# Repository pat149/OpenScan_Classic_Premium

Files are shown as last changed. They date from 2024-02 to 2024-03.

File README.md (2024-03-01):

# OpenScan Classic Premium
Completely redesigned version of the OpenScan Classic by Thomas Megel ([ @github/OpenScan-org ](https://github.com/OpenScan-org)).

> [!CAUTION]
> This version is still work in progress. There's no guarantee everything works as intended. I'm expecting to do the full testing until the middle of February.

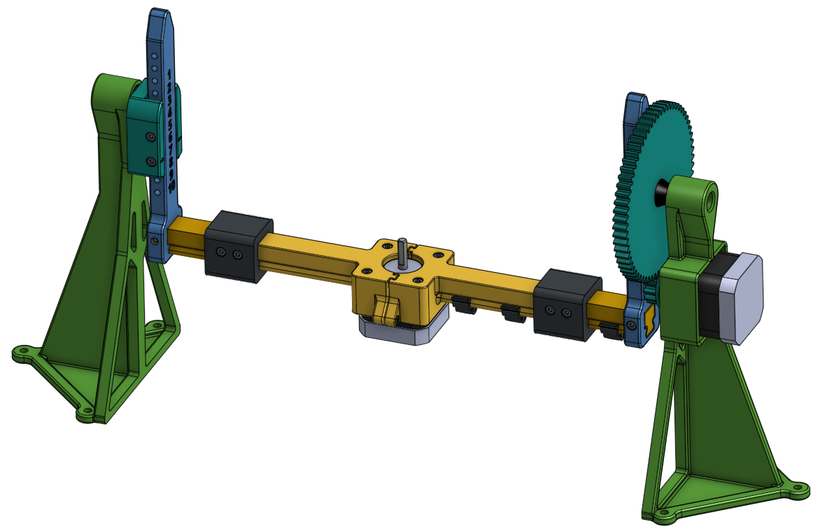
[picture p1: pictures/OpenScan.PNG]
OpenScan Classic Premium


## Introduction
The intentions behind the redesign of the OpenScan Classic were that it seems it has never gotten out of it's prototype stage constructionwise.
So I made a list with things that should be improved.

- sturdier overall construction
- more convenient height adjustment
- use ball bearings instead of pins
- use heated inserts instead of driving the screw into the plastic
- higher modularity concerning the size of the scanner
- cable management for the turntable stepper
- printing without any supports
- higher quality looking finish

So I redesigned the Classic version from scratch on and the result was the OpenScan Classic Premium (might change the name in the future). No parts of the original mainframe have been reused in order to make room for improvements while simultaneously keeping the original shape and functionality.
Because I don't use a PiCam I didn't redesigned the stand for the Raspberry Pi (yet).

## Bill of material
This BOM represents the bare minimum of material without using any extensions on the arms.
| Part  | Quantity |
| --- | --- |
| M3x8 (ISO 4762) | 8  |
| M3x10 (ISO 4762) | 2  |
| M3x25 (ISO 4762) | 2  |
| M3x30 (ISO 4762) | 4  |
| M5x20 (ISO 4762) | 1  |
| M5x25 (ISO 4762)| 1  |
| Washer M5  | 2  |
| Heated Insert M3x4  | 8  |
| Heated Insert M5x6  | 2  |
| Ball bearing 625-2RS  | 4  |
| Nema 17 Stepper Motor (>13Ncm)  | 1  |
| Nema 17 Stepper Motor (>40Ncm)  | 1  |
| Stand1_Nema17.step  | 1  |
| Stand2.step  | 1  |
| Spacer_Adapter_Gear.step (Measure shaft stick out for correct version)  | 1  |
| Gear_Small.step  | 1  |
| Adapter_Gear.step  | 1  |
| Adapter.step  | 1  |
| Rotary_Arm.step  | 2  |
| Turntable_Base1.step  | 1  |
| Turntable_Base2.step  | 1  |

## Print settings
Every part can be printed without any supports at all using the following print settings:
- 0.4mm nozzle
- 0.2mm layer height
- 3 walls (except for Turntable_Base, Turntable_Extension and Rotary_Arm: min. 5 walls, depending on the overall length)
- 15% infill

## Assembly instructions
For a detailed step by step instruction go to the dedicated instructions folder above.
For those only interested in the assembly order here are some exploded views of the OpenScan Classic Premium.

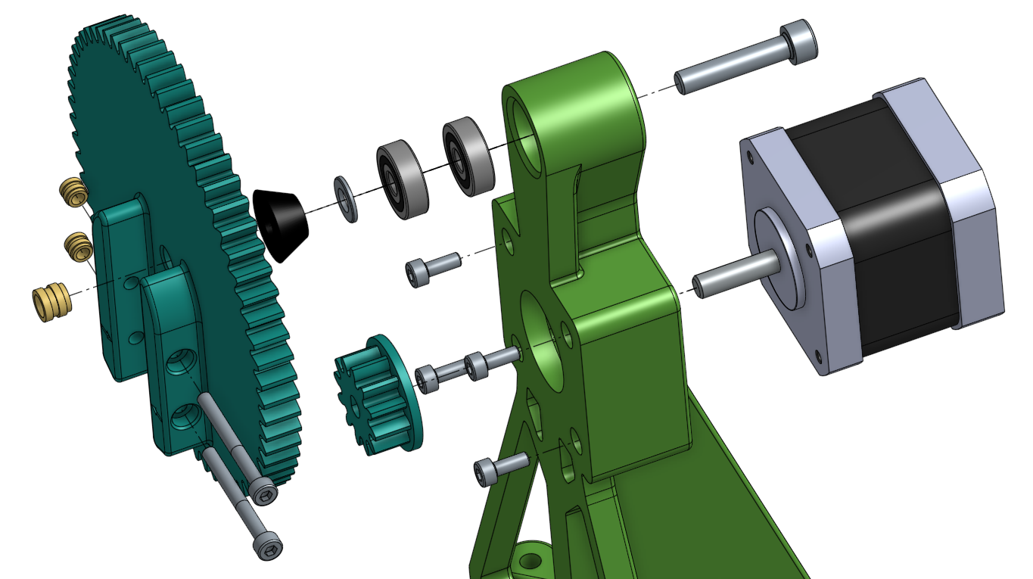
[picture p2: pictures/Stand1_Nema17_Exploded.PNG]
Assembly of the motor stand

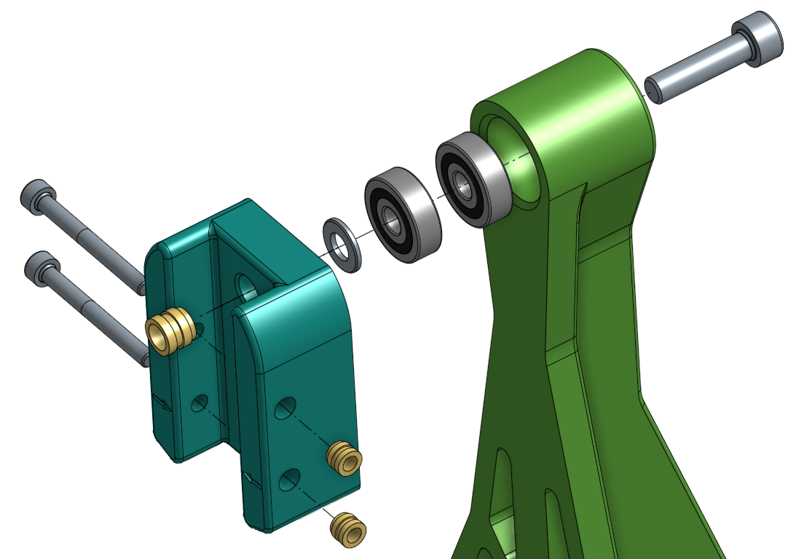
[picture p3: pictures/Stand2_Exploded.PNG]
Assembly of the stand 2

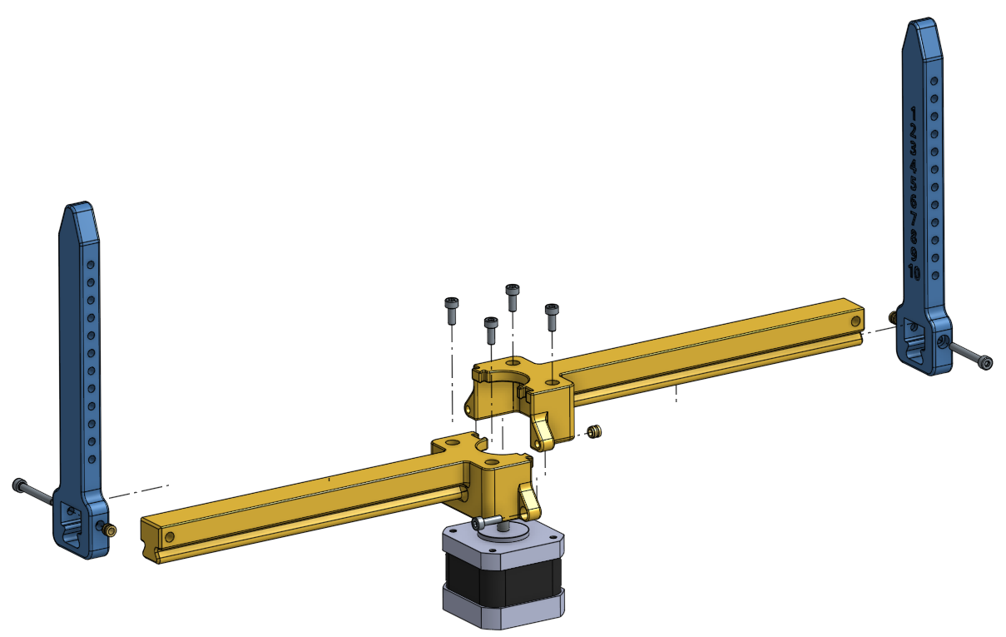
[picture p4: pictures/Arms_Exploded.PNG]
Assembly of the arms


## To-do-list
- [ ] Adding more rigidity to the turntable stepper frame mount
- [ ] Create a heavy duty version

## Changelog
- 1st March, 2024: reuploaded all *.stl with correct scale

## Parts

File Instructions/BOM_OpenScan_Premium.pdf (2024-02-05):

Description | Quantity
Hex socket head screw M3x8 | 8
Hex socket head screw M3x10 | 2
Hex socket head screw M3x25 | 2
Hex socket head screw M3x30 | 4
Hex socket head screw M5x20 | 1
Hex socket head screw M5x25 | 1
Washer M5 | 2
Heated Insert M3x4 | 8
Heated Insert M5x6 | 2
Ball bearing 625-2RS | 4
Nema 17 Stepper Motor (>13Ncm) | 1
Nema 17 Stepper Motor (>40Ncm) | 1
Stand1_Nema17.step | 1
Stand2.step | 1
Spacer_Adapter_Gear.step (Measure shaft stick out for correct version) | 1
Gear_Small.step | 1
Adapter_Gear.step | 1
Adapter.step | 1
Rotary_Arm.step | 2
Turntable_Base1.step | 1
Turntable_Base2.step | 1

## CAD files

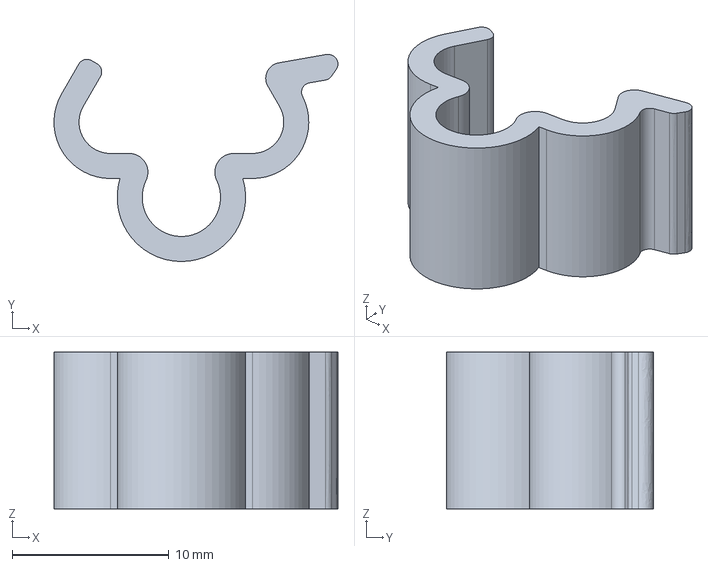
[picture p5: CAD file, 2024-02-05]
STEP/Cable_Clip.step
18.1 x 13.2 x 10.0 mm

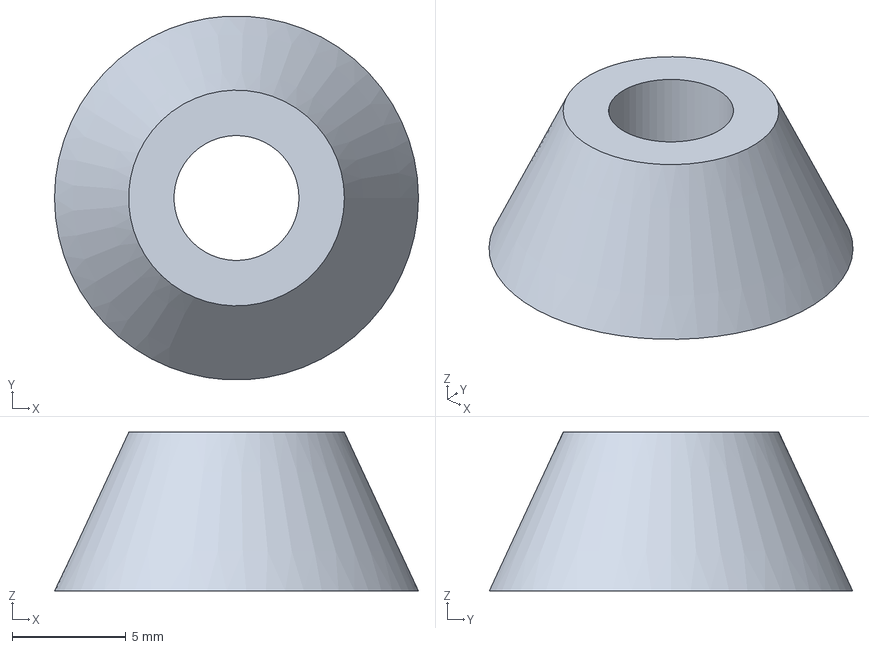
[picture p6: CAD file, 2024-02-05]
STEP/Spacer_Adapter_Gear/Spacer_Adapter_Gear_15mm.step
16.0 x 16.0 x 7.00 mm

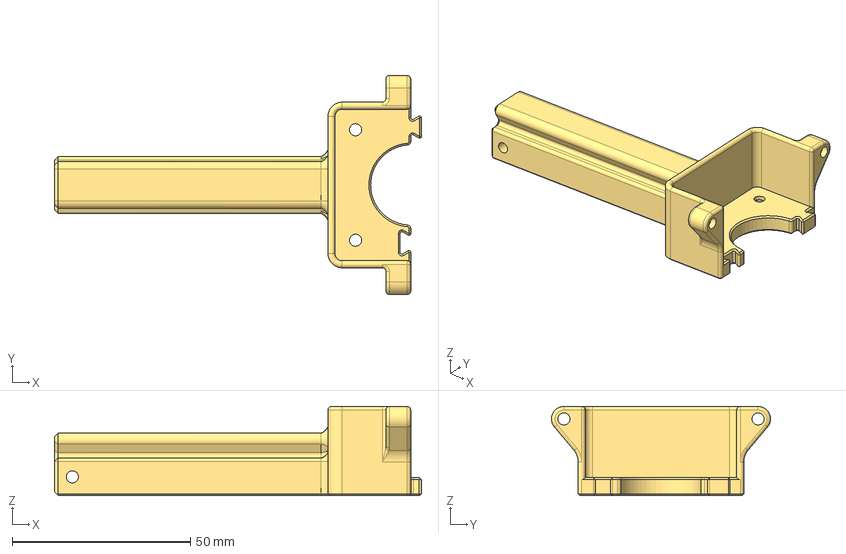
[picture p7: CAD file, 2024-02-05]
STEP/Turntable_Base1/Turntable_Base1_100mm.step
103.0 x 61.5 x 25.0 mm

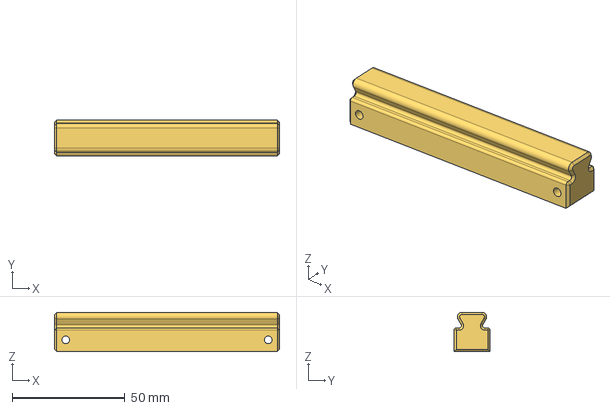
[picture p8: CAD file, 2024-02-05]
STEP/Turntable_Extension/Turntable_Extension_100mm.step
100.0 x 16.0 x 17.5 mm

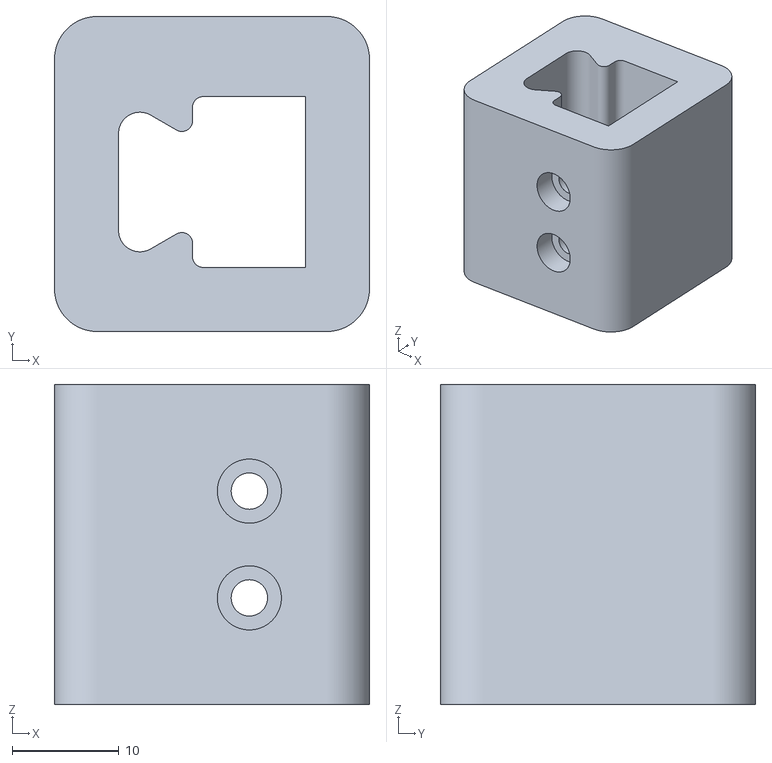
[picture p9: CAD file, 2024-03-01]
STL/Extension_Connector.stl
29.5 x 29.5 x 30.0

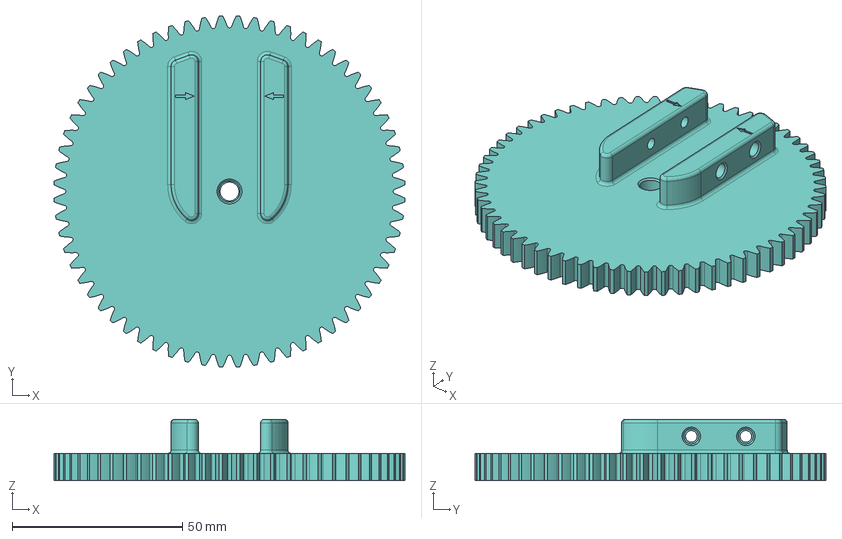
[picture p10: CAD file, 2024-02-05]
STEP/Adapter_Gear.step
103.0 x 103.0 x 18.0 mm

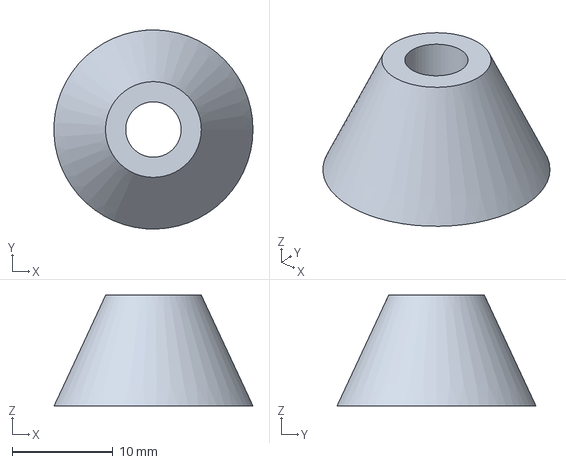
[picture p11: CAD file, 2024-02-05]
STEP/Spacer_Adapter_Gear/Spacer_Adapter_Gear_19mm.step
19.7 x 19.8 x 11.0 mm

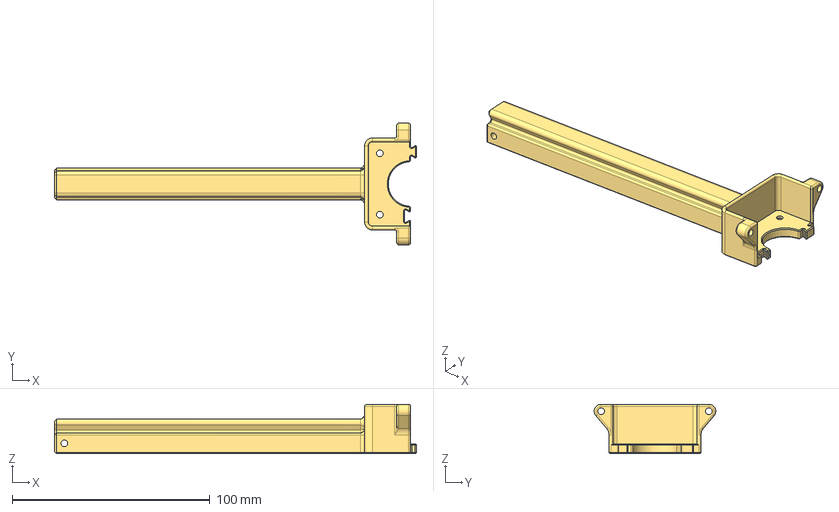
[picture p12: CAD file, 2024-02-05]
STEP/Turntable_Base1/Turntable_Base1_180mm.step
183.0 x 61.5 x 25.0 mm

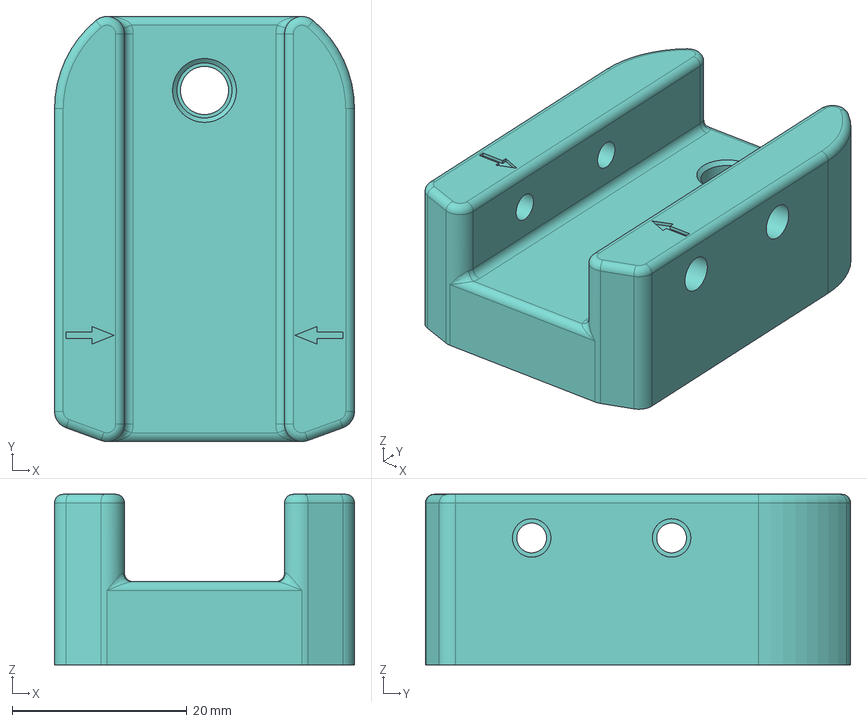
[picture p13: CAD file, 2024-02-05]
STEP/Adapter.step
34.3 x 48.6 x 19.5 mm

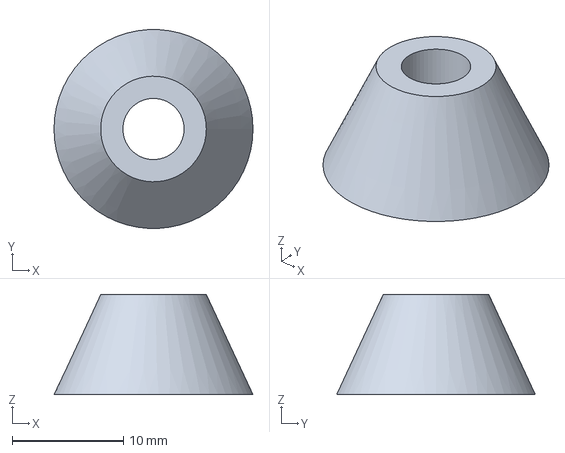
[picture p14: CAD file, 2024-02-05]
STEP/Spacer_Adapter_Gear/Spacer_Adapter_Gear_17mm.step
17.9 x 17.9 x 9.00 mm

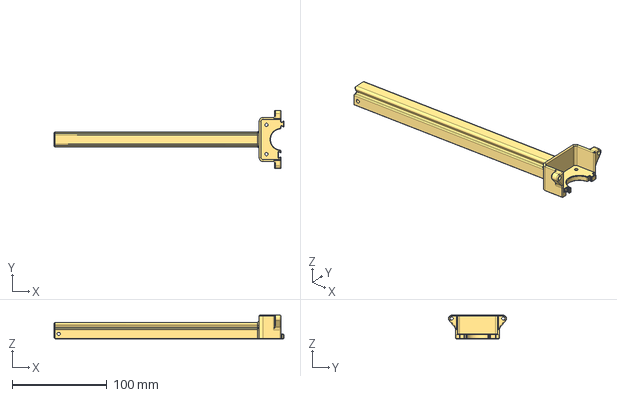
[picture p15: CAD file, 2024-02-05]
STEP/Turntable_Base1/Turntable_Base1_240mm.step
243.0 x 61.5 x 25.0 mm

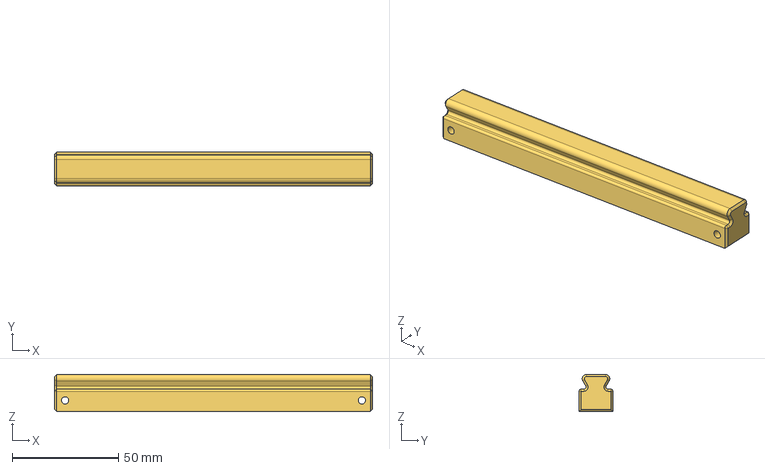
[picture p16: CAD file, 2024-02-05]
STEP/Turntable_Extension/Turntable_Extension_150mm.step
150.0 x 16.0 x 17.5 mm

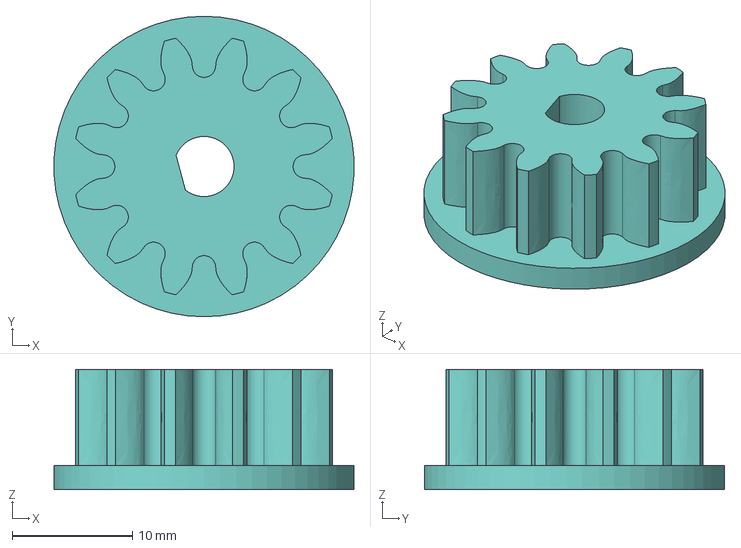
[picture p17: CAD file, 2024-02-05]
STEP/Gear_Small.step
25.0 x 25.0 x 10.0 mm

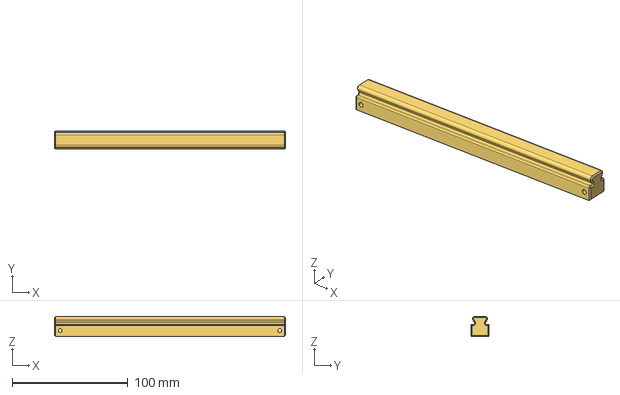
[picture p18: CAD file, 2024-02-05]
STEP/Turntable_Extension/Turntable_Extension_200mm.step
200.0 x 16.0 x 17.5 mm

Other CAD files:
STEP/Turntable_Base2/Turntable_Base2_100mm.step
STEP/Turntable_Base2/Turntable_Base2_180mm.step
STEP/Turntable_Extension/Extension_Connector.step
STEP/Turntable_Base2/Turntable_Base2_240mm.step
STEP/Rotary_Arm.step
STEP/Stand1_Nema17.step
STEP/Stand2.step
STEP/Turntable_Extension/Turntable_Extension_50mm.step
STL/Adapter.stl
STL/Adapter_Gear.stl
STL/Cable_Clip.stl
STL/Gear_Small.stl
STL/Rotary_Arm.stl
STL/Spacer_Adapter_Gear/Spacer_Adapter_Gear_15mm.stl
STL/Spacer_Adapter_Gear/Spacer_Adapter_Gear_17mm.stl
STL/Spacer_Adapter_Gear/Spacer_Adapter_Gear_19mm.stl
STL/Turntable_Base1/Turntable_Base1_240mm.stl
STL/Turntable_Extension/Turntable_Extension_100mm.stl
STL/Turntable_Extension/Turntable_Extension_150mm.stl
STL/Turntable_Extension/Turntable_Extension_200mm.stl
STL/Turntable_Extension/Turntable_Extension_50mm.stl

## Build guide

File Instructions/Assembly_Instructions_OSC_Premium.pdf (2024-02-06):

## Assembly instructions for

# OpenScan Classic Premium

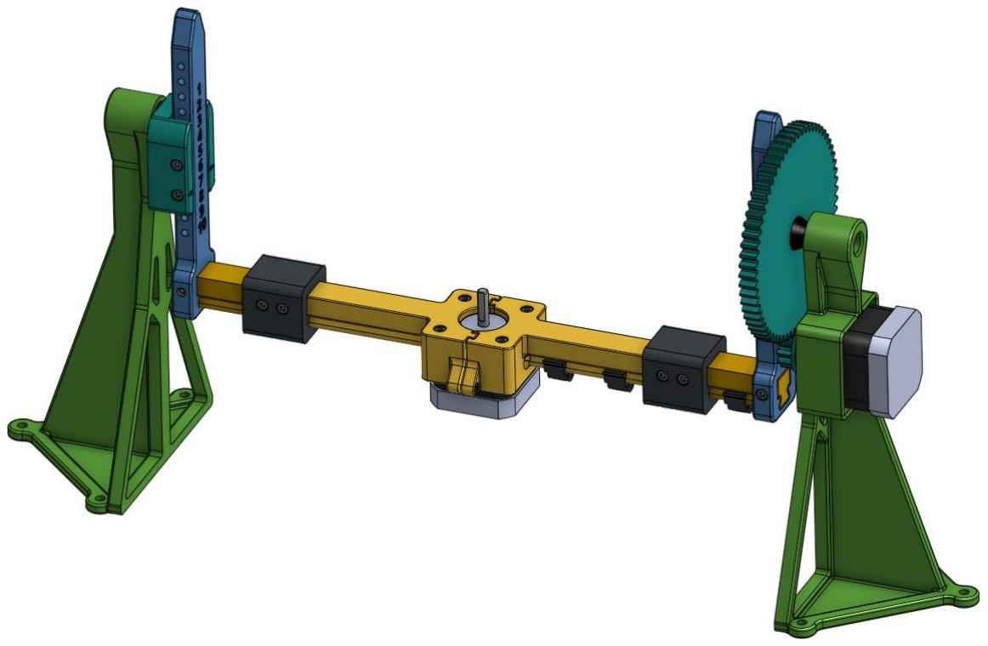
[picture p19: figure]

Description | Quantity
Hex socket head screw M3x8 | 8
Hex socket head screw M3x10 | 2
Hex socket head screw M3x25 | 2
Hex socket head screw M3x30 | 4
Hex socket head screw M5x20 | 1
Hex socket head screw M5x25 | 1
Washer M5 | 2
Heated Insert M3x4 | 8
Heated Insert M5x6 | 2
Ball bearing 625-2RS | 4
Nema 17 Stepper Motor (>13Ncm) | 1
Nema 17 Stepper Motor (>40Ncm) | 1
Stand1_Nema17.step | 1
Stand2.step | 1
Spacer_Adapter_Gear.step (Measure shaft stick out for correct version) | 1
Gear_Small.step | 1
Adapter_Gear.step | 1
Adapter.step | 1
Rotary_Arm.step | 2
Turntable_Base1.step | 1
Turntable_Base2.step | 1

# Assembly of the standard version

(assembly of the extensionsions see pages 20-23)

## Bill of material (BOM)

## Overview

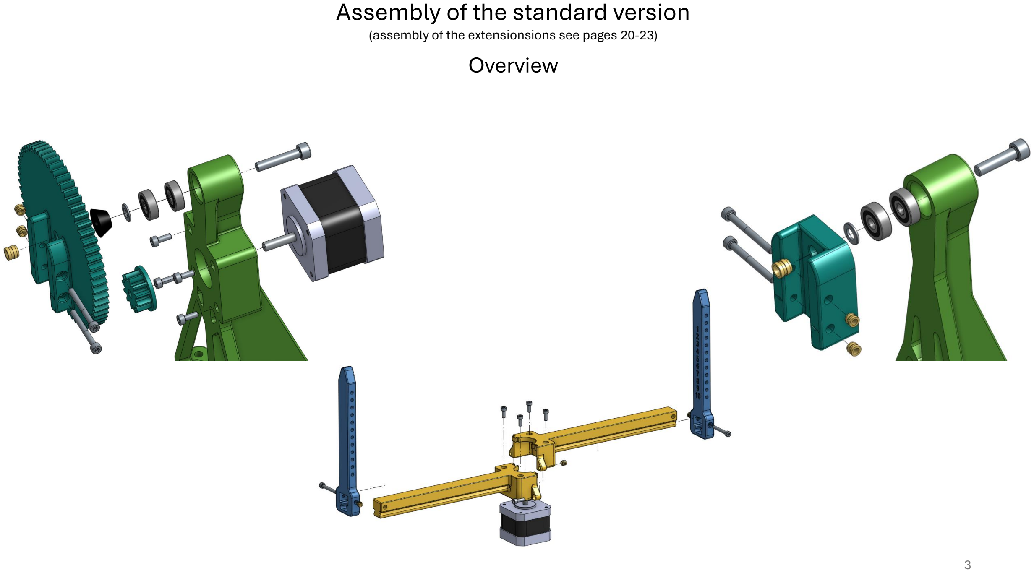
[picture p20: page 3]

(assembly of the extensionsions see pages 20-23)

4x

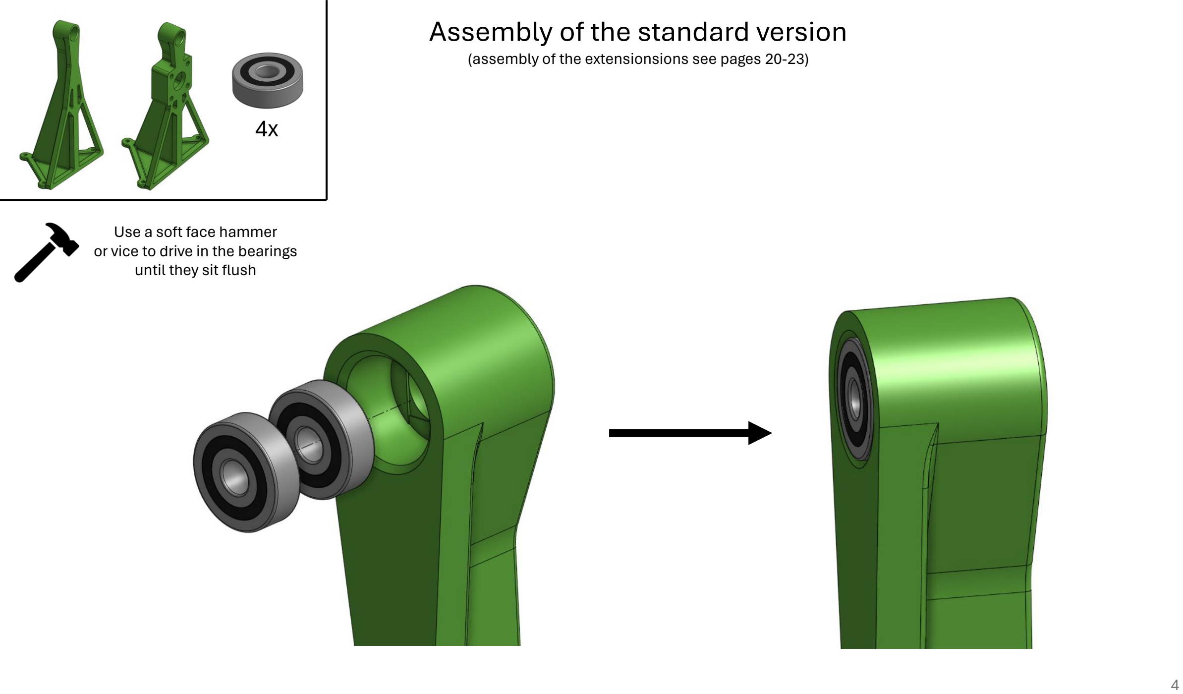
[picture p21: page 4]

(assembly of the extensionsions see pages 20-23)

Use a soft face hammer
or vice to drive in the bearings until they sit flush

(assembly of the extensionsions see pages 20-23)

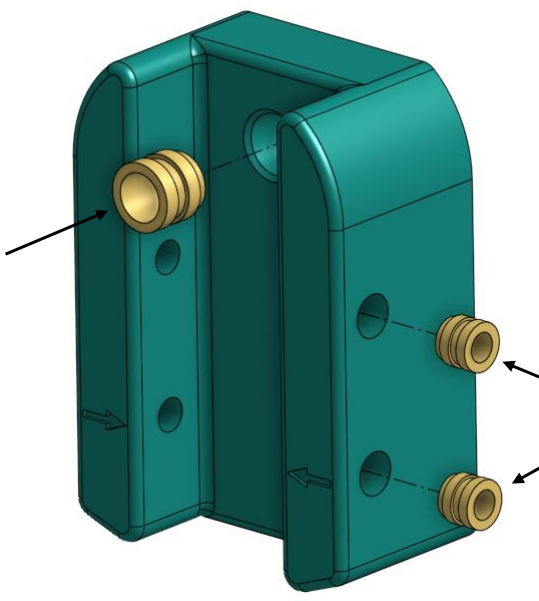
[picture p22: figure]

Use a soldering iron to put in the heated inserts (Temperature: print temperature +10%)

2x
M3x4

1x
M5x6

M5x6

M3x4

(assembly of the extensionsions see pages 20-23)

2x
M3x4
2x

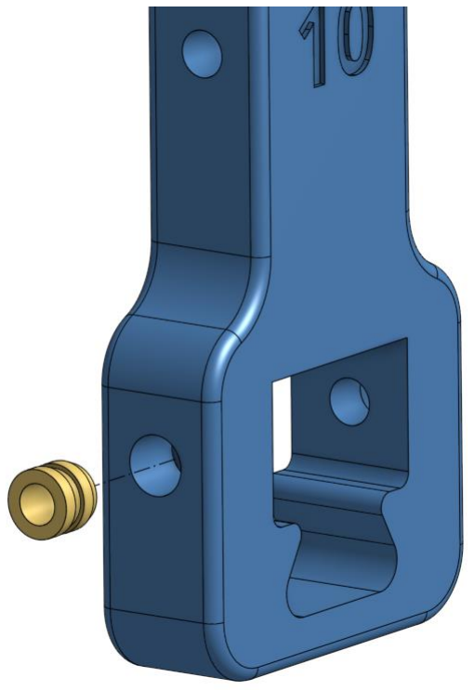
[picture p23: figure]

Use a soldering iron to put in the heated inserts (Temperature: print temperature +10%)

2x
M3x4

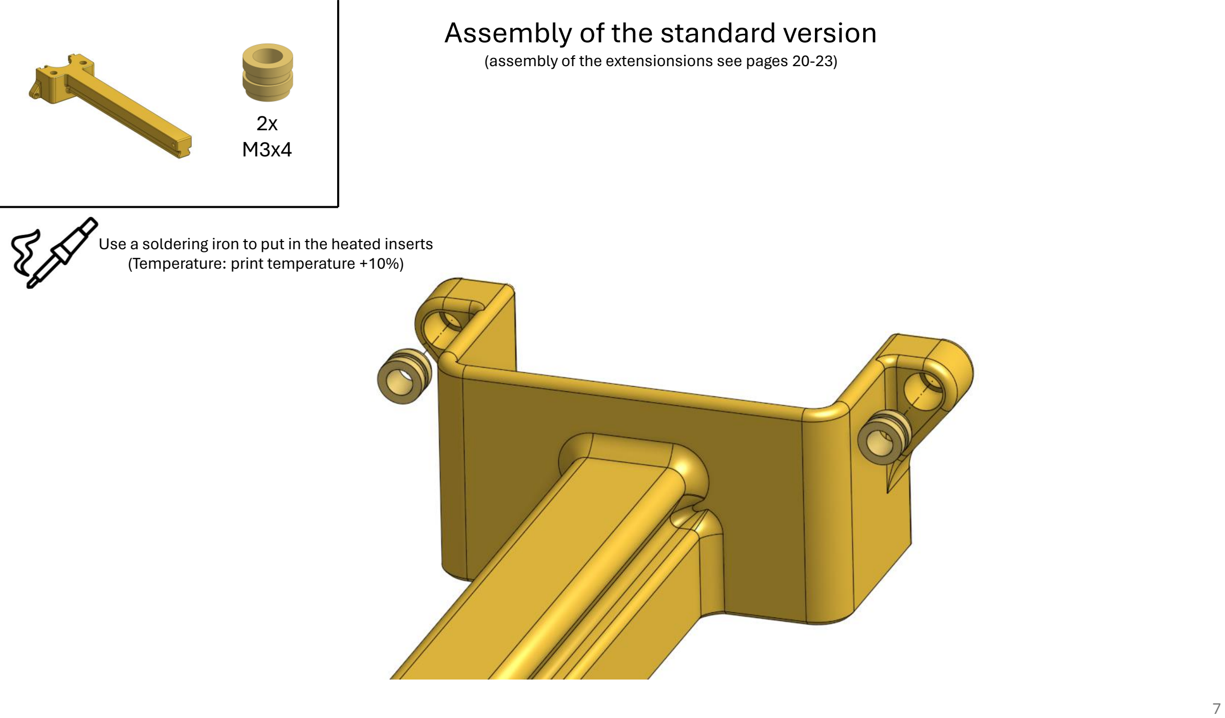
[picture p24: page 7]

(assembly of the extensionsions see pages 20-23)

Use a soldering iron to put in the heated inserts (Temperature: print temperature +10%)

(assembly of the extensionsions see pages 20-23)

2x
M3x4

1x
M5x6

M3x4

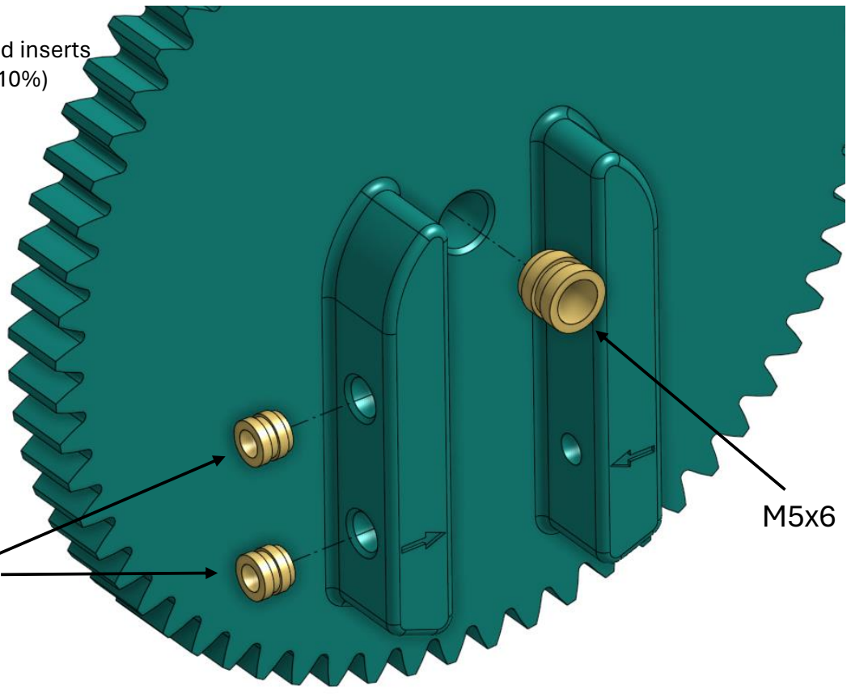
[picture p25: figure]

Use a soldering iron to put in the heated inserts (Temperature: print temperature +10%)

4x

## M3x8 >40 Ncm

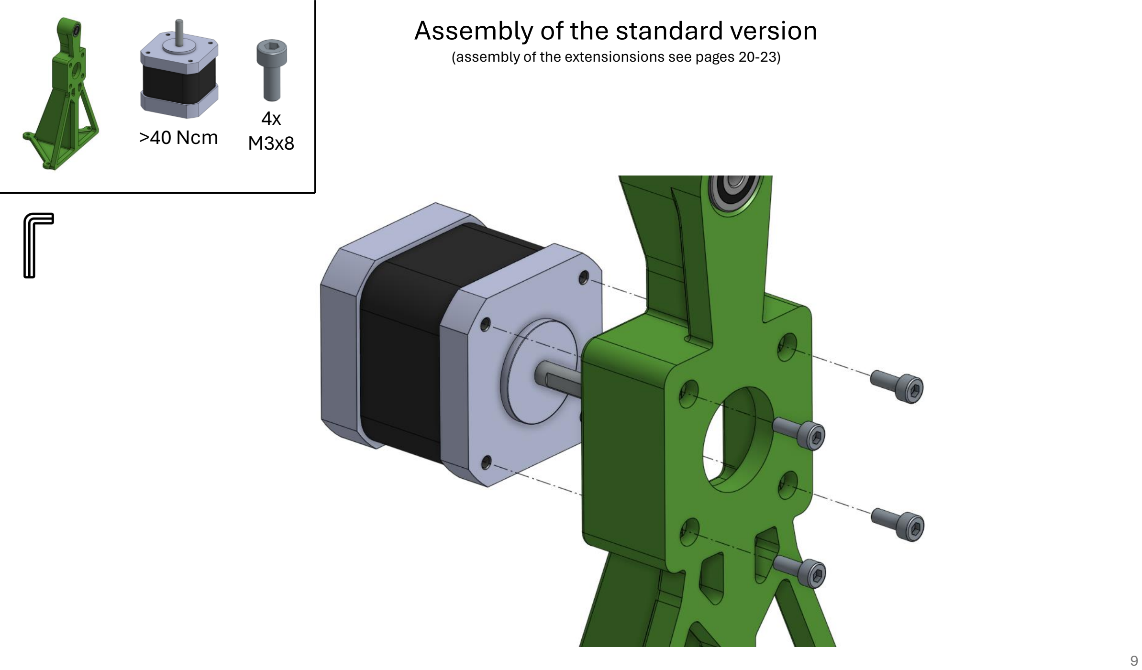
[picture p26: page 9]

(assembly of the extensionsions see pages 20-23)

(assembly of the extensionsions see pages 20-23)

Measure the stick out of the stepper motor shaft from the face of the printed stand.

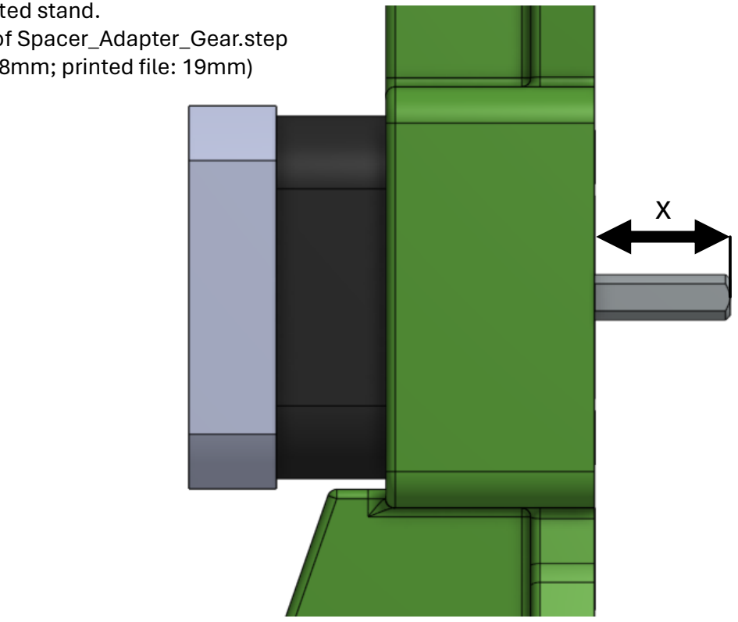
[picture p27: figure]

Print the next bigger version of Spacer_Adapter_Gear.step (e.g. measured value: 17.8mm; printed file: 19mm)

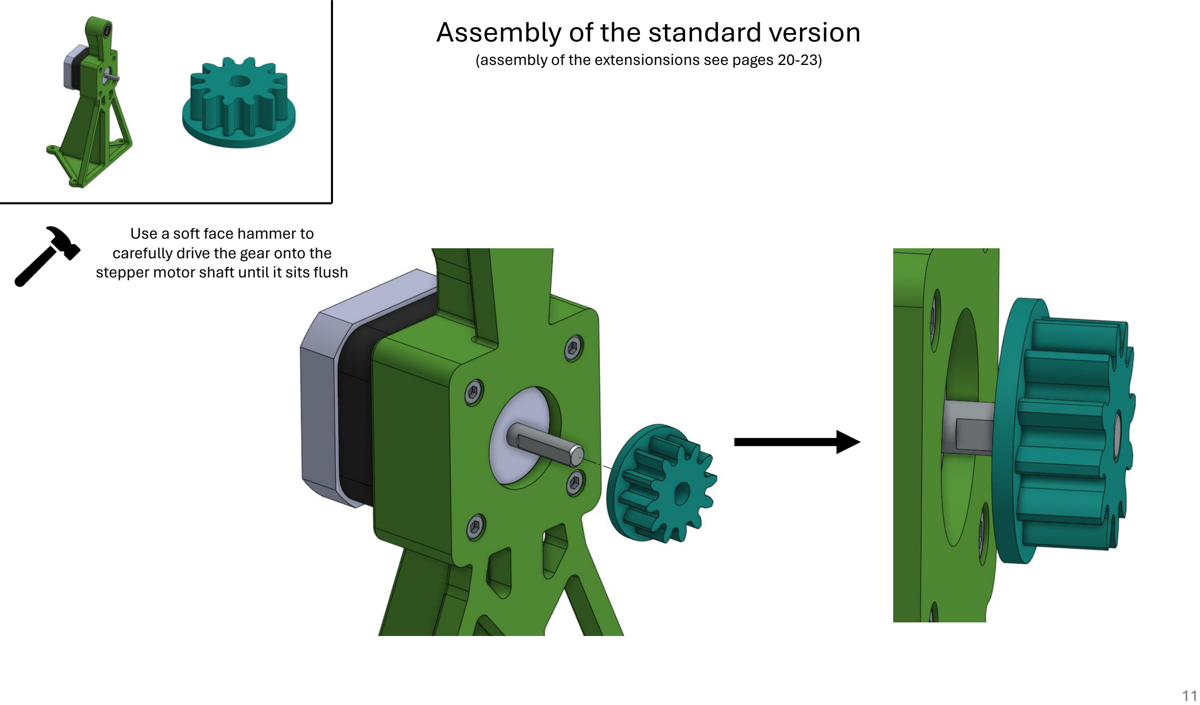
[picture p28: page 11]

(assembly of the extensionsions see pages 20-23)

Use a soft face hammer to
carefully drive the gear onto the stepper motor shaft until it sits flush

M5x25

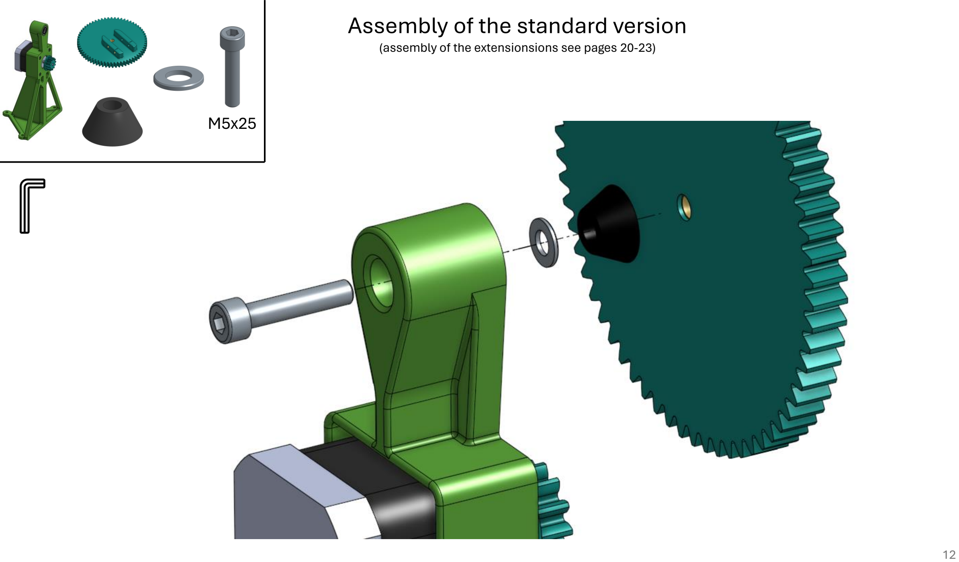
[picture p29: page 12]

(assembly of the extensionsions see pages 20-23)

(assembly of the extensionsions see pages 20-23)

M5x20

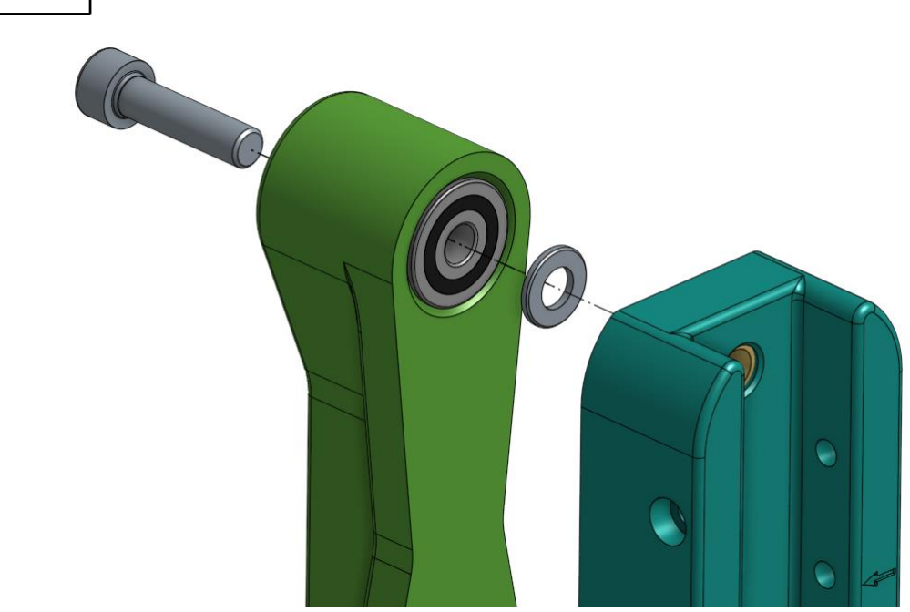
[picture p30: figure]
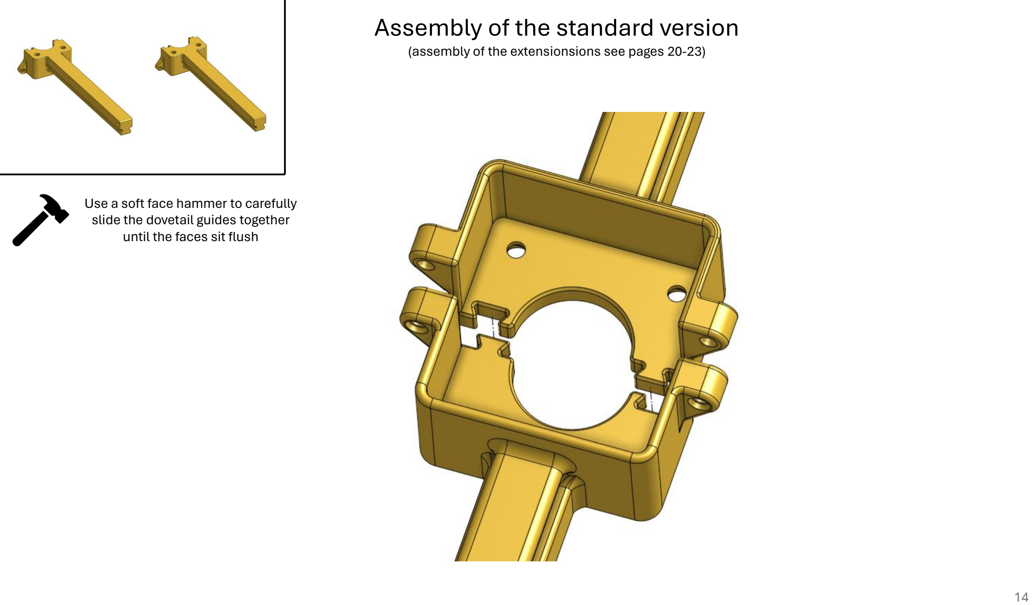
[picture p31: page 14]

(assembly of the extensionsions see pages 20-23)

Use a soft face hammer to carefully slide the dovetail guides together until the faces sit flush

2x
M3x10

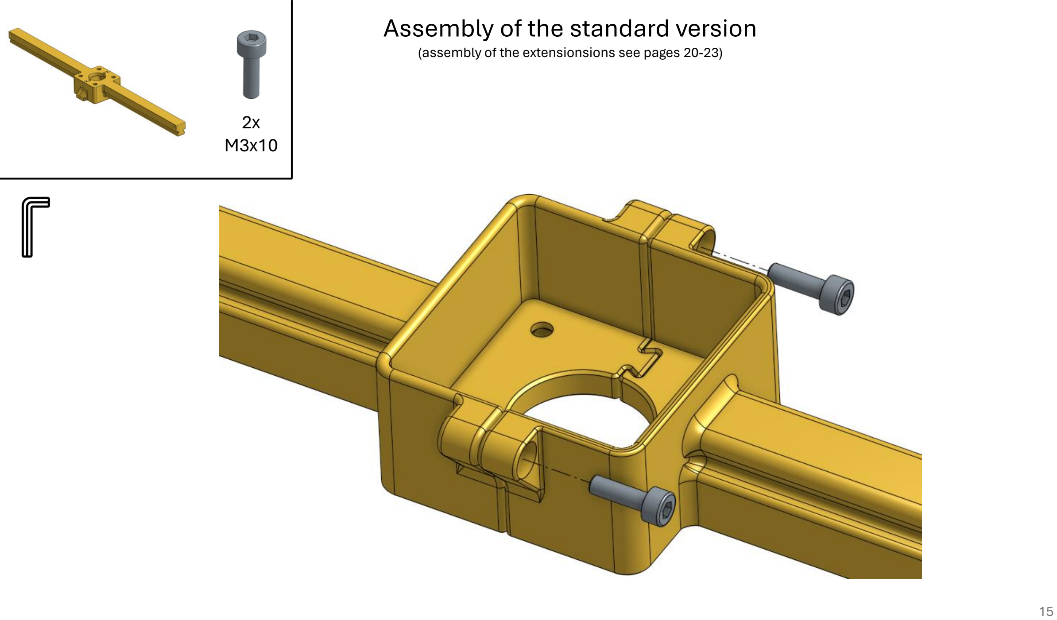
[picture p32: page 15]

(assembly of the extensionsions see pages 20-23)

(assembly of the extensionsions see pages 20-23)

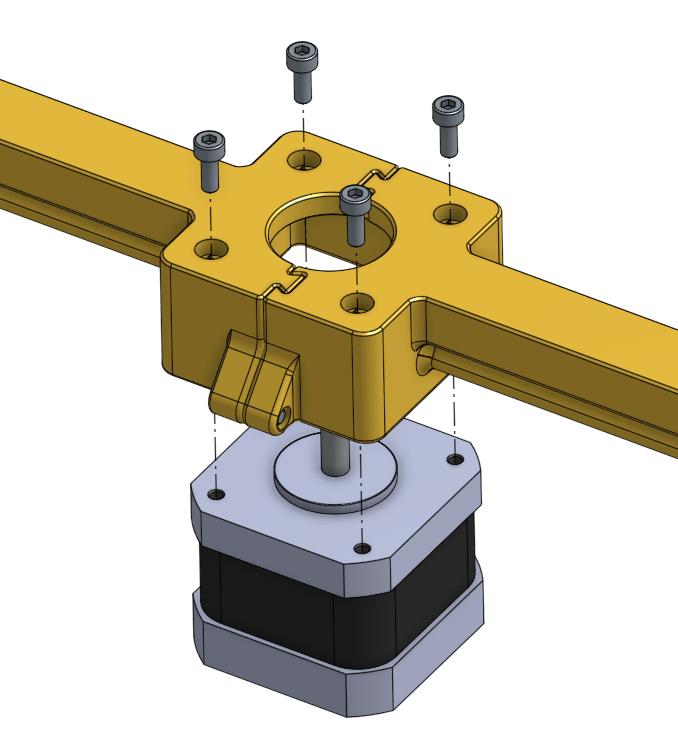
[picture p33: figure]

4x

## M3x8 >13 Ncm

(assembly of the extensionsions see pages 20-23)

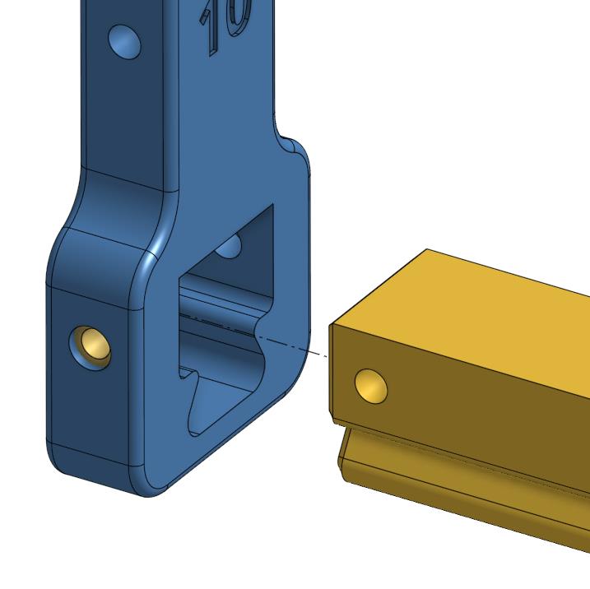
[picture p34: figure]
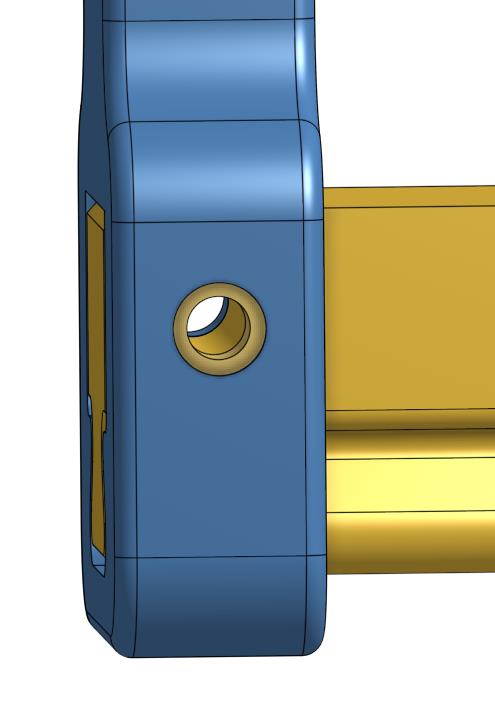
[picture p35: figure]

2x

Use a soft face hammer to carefully slide the arm over the beam until it sits flush. The numbered side of the arm should face the stepper motor!

2x
M3x25

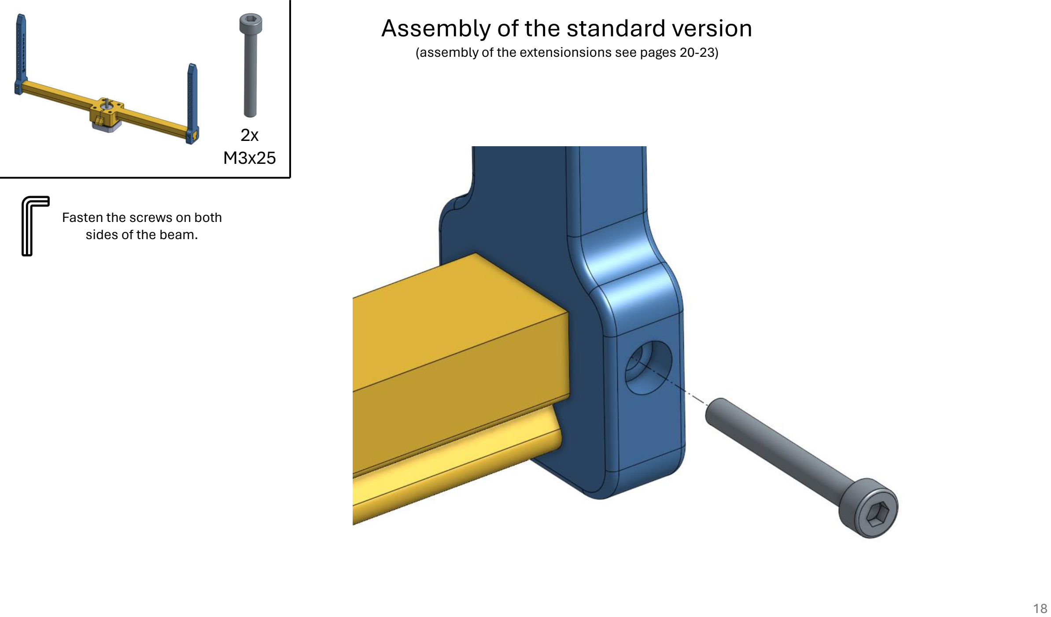
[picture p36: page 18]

(assembly of the extensionsions see pages 20-23)

Fasten the screws on both
sides of the beam.

(assembly of the extensionsions see pages 20-23)

4x
M3x30

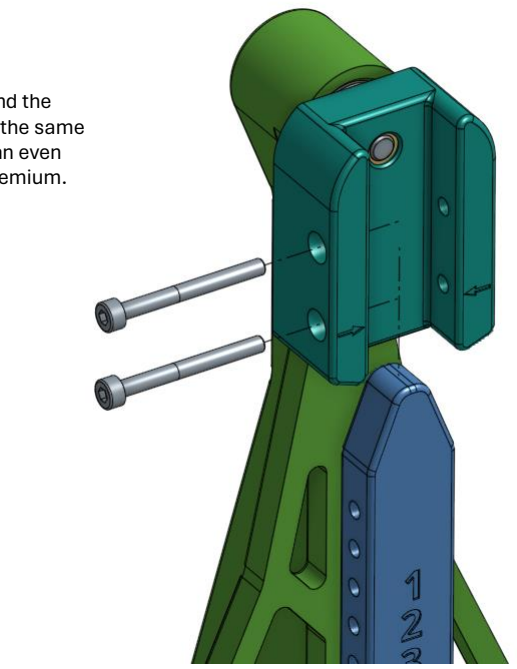
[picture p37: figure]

Slide the arms into the guides of the adapter and the adapter gear. Make sure the arrows match up with the same number on the arms on both sides to maintain an even height on both sides of the OpenScan Classic Premium.

Done! Your OpenScan Classic Premium should now look something like this.

# Great job!

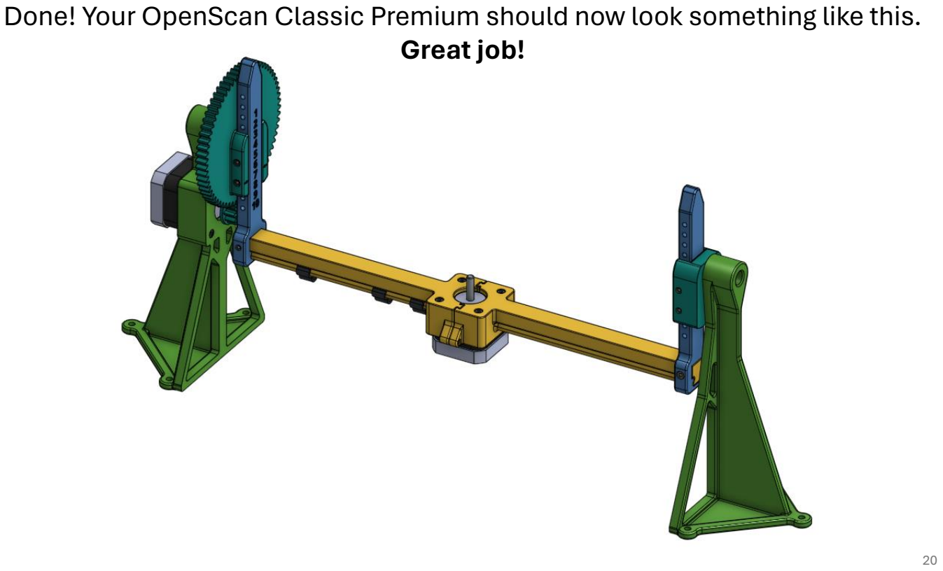
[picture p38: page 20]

# Assembly of the extension arms

# Bill of material (BOM)

(For each single extension used, usually you will need one per side)

Description | Quantity
Hex socket head screw M3x25 | 2
Heated Insert M3x4 | 2
Turntable_Extension.step | 1
Extension_Connector.step | 1

# Assembly of the extension arms

2x
M3x4

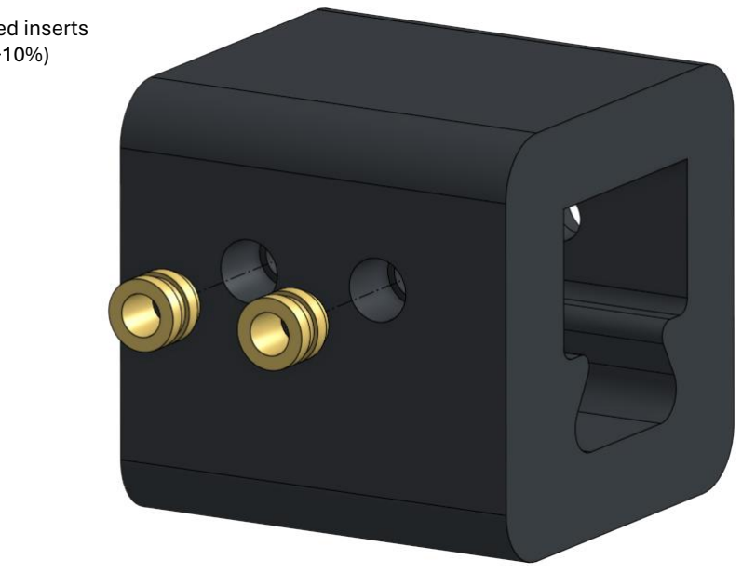
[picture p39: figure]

Use a soldering iron to put in the heated inserts (Temperature: print temperature +10%)

# Assembly of the extension arms

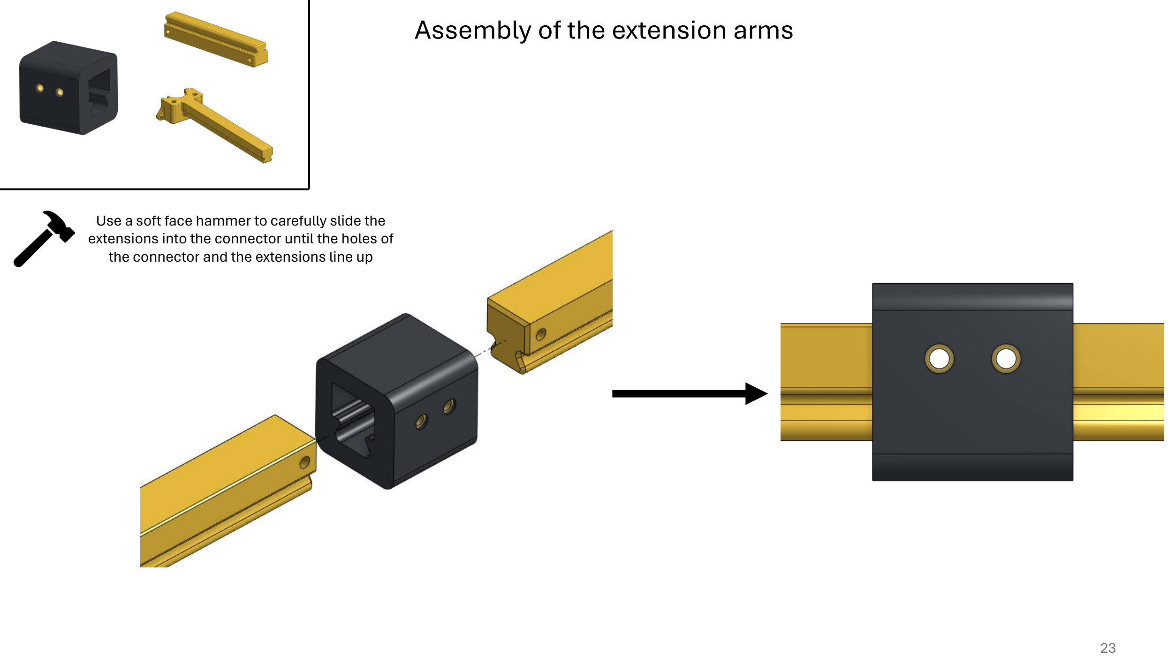
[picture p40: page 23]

Use a soft face hammer to carefully slide the extensions into the connector until the holes of the connector and the extensions line up

# Assembly of the extension arms

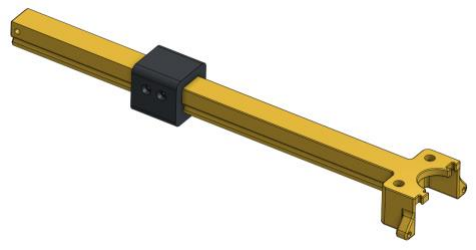
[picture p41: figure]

2x
M3x25

# Cable Management

## Especially when using a DSLR camera with the pi standing next to the model rig you can use these clips on the underside of the main beam

to clean up your cable management.

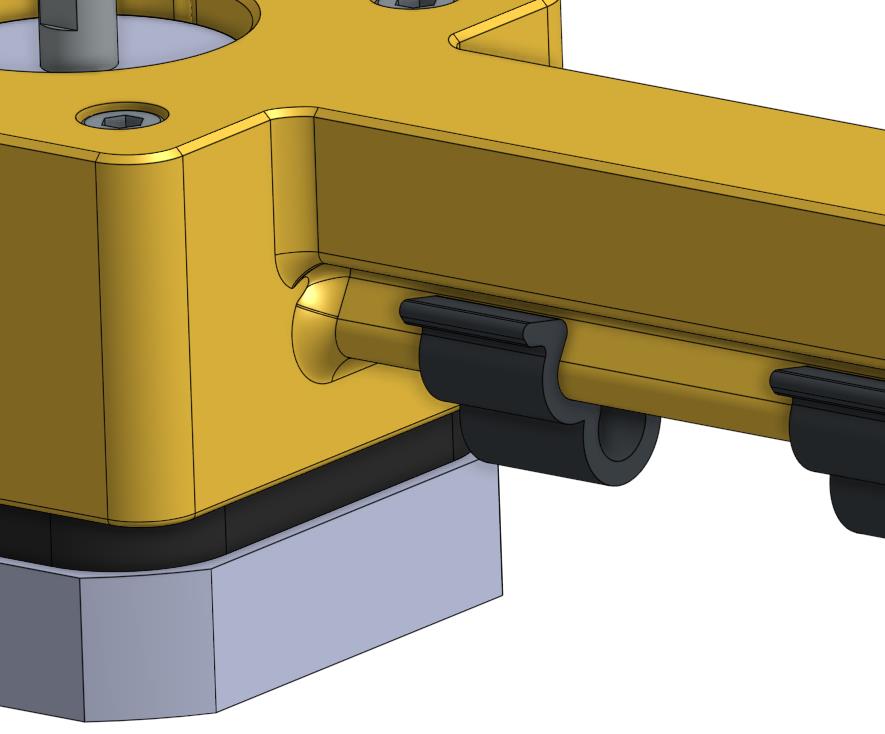
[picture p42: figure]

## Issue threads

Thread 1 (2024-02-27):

Alternative Turntable Base

BigStotty, 2024-02-27:
Due to get my parts soon and came across your work that looks like what i am interested in but i was thinking perhaps an alternative centre to allow easier printing and bars to start at this point. Not sure what this would do to strength
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

pat149, 2024-02-27:
Hey Stotty,
that looks pretty good. I was thinking about a similar version, because the strength of the sidewall of my version is the weak point, when the stepper motor gets warm. Especially when printing in PLA.
That could be a great alternative, because the flexing sidewalls are way thicker than mine. Maybe I‘ll consider designing a similar version with some small tweaks to add more rigidity.
But I have to say: I think it‘s a little harder to print because of the floating areas within the connectors. I‘ll think about your input. Thanks very much.

BigStotty, 2024-02-27:
Only way i can think of overcoming that would be to completely redesign your connectors, but i will leave it with you.
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

MrMxyzptlk, 2024-11-27:
How about just adding a pc fan under the motor to keep it cool?

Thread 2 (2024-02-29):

Most/All STLs have the wrong scale

probably-Erwins-Cat, 2024-02-29:
It seems that the exported STLs are too small, approximately a factor of 10. This should be checked, e.g. the spacing of nema17 mounting points provide the right scale factor.

BigStotty, 2024-02-29:
Spot checking and STEP are fine, STL output looks like its been doing in M rather than mm

pat149, 2024-03-01:
Thanks for your hint. I reexported the parts so the *.stl's it should be the correct size.

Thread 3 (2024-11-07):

Question: I ordered the OpenScan Classic 'kit' minus the 3d prints...where do I mount the electronics / camera, etc in your version?

MrMxyzptlk, 2024-11-07:
Question: I ordered the OpenScan Classic 'kit' minus the 3d prints...where do I mount the electronics / camera, etc in your version?

Thanks for your work!

pat149, 2024-11-07:
Hey,

the Raspberry stand has to be used from the original version. The camera stand you have to purchase or print by yourself, depending on which camera you want to use. I might think about updating the design so that the Raspberry can be mounted directly onto the stand. But the last year was really busy and probably the coming year will be too.

MrMxyzptlk, 2024-11-07:
Thank you! I'm using the autofocus Arducam IMX519

MrMxyzptlk, 2024-11-07:
Does this look like the right part to print for the rPi, Arducam, and network?

pat149, 2024-11-07:
That‘s one part of it, yes. There‘s another repository where you can download the rest of the scanner. I‘ll put the link below.
You‘ll need the correct Pi-Shield-stl and the Turntable-Adapter. Everything else should be provided with my new design.

https://github.com/OpenScan-org/OpenScan-Design/tree/main/STL/Classic/V1

MrMxyzptlk, 2024-11-13:
Thanks.

Closed 2024-11-13.
